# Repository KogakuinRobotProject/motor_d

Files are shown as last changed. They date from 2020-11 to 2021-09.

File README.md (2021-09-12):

# 直流モータドライバ基盤
## 仕様　<br>
to252のFETに対応している。用件によって必要となる定格のFETを使うこと<br>
PWMfreqは20kHz～50kHz(100kHzとかでも動くだろうけど、スイッチング損失えぐい)<br>

|FaultFlag|LEDstate|
|---|---|
|FF1|Green|
|FF2|Red|

<br>

|FF1state|FF2state|MDstate|
|---|---|---|
|0|0|Normal Operation|
|1|0|Overtemperature|
|0|1|Short-to-ground,Short-to-supply,Shorted load|
|1|1|V5 undervoltage,VREG undervoltage,Bootstrap undervoltage|

## FET使用例（FETゲート回路周りの定数）

|MOSFETname|Gate Register|Gate to Source Capasita|
|----|----|----|
|IPD034N06N3G|10|220~1000pF|
|DMTH4005SK3Q|10|1000~2200pF|

## 注意
FETを変えた場合ゲート入力抵抗、GS間容量(C_add)を適切な値に変更すること。目安は下記 <br>
<a href="https://www.codecogs.com/eqnedit.php?latex=\frac{C_{dg}}{C_{gs}&plus;C_{add}}&space;=&space;0.5" target="_blank">\frac{C_{dg}}{C_{gs}+C_{add}} = 0.5</a> <br>
上式で容量を決めたらオシロスコープでFETの立ち下がりを見てセルフターンオンしないゲート入力抵抗を入れる <br>
基板上のC_5,C_6の値をFETの追加容量含んだトータルゲートチャージの10倍ほどのコンデンサに変更する<br>
※データシート上では容量ではなく、充電される電荷が記載されているため、電荷にV_gsを徐算すること<br>
※セルフターンオンしているとDtimeでカバーできない上下アームオン状態が生まれ、短絡しFETの発熱およびドライバの短絡検知、電流制限に引っかかる。<br>
※セルフターンオンであると思っていたものがそうでなかった。低負荷状態ではセルフターンオンの発生は確認できなかったが、高負荷時に発生する可能性があるため上記目安を参考に容量を追加すること。<br>

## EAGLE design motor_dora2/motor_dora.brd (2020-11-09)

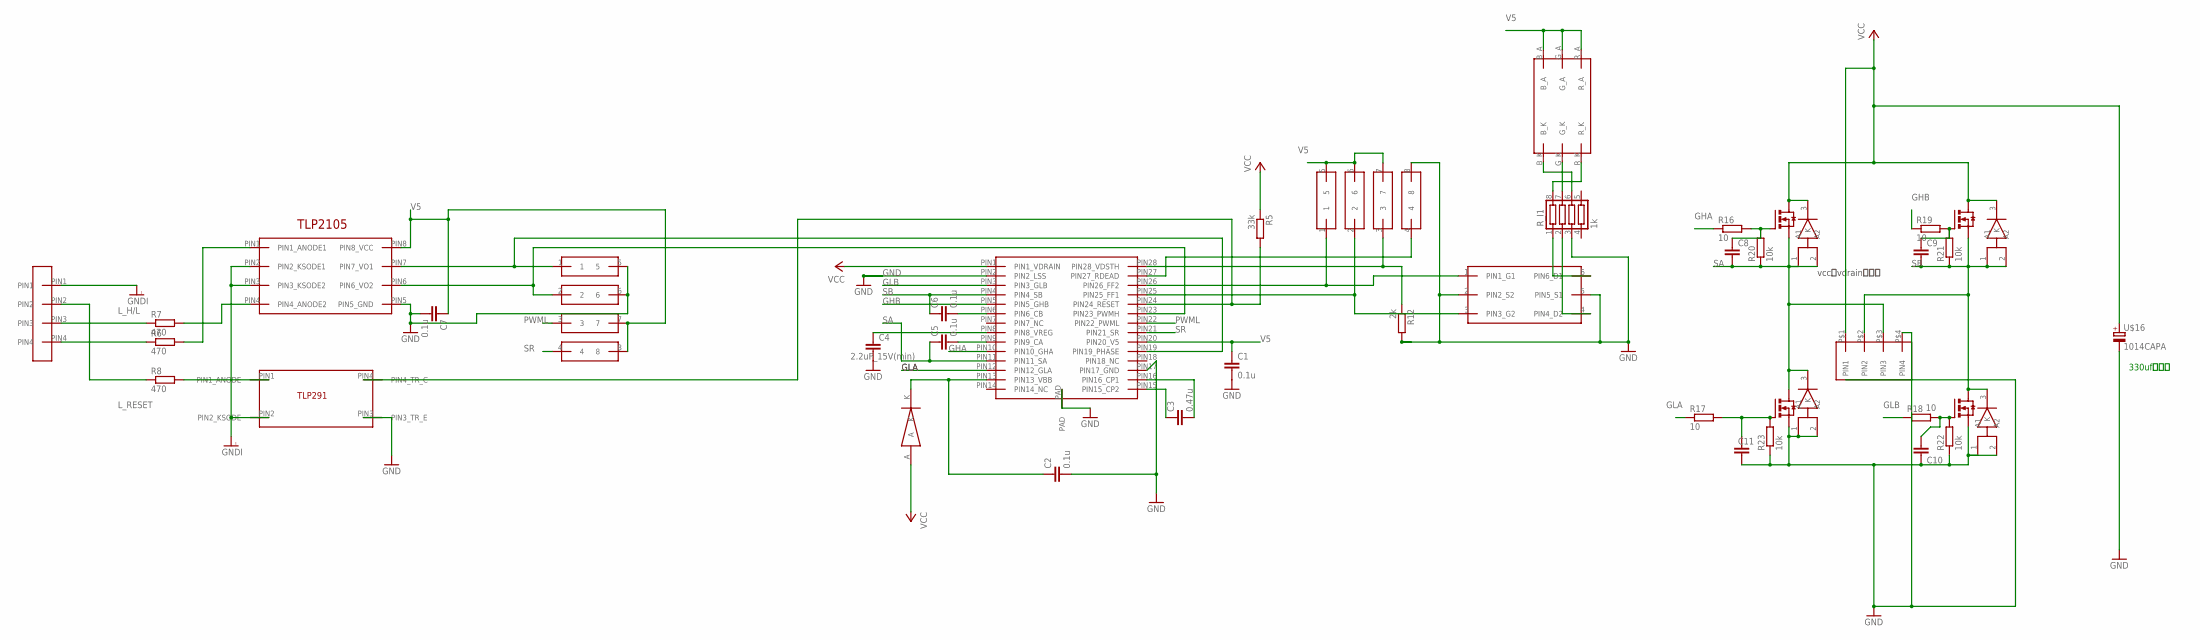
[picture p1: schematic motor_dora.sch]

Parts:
C1, C2, C5, C6, C7: 0.1u; C2012
C3: 0.47u; C2012
C4: 2.2uF_15V(min); C2012
C8, C9, C10, C11: C-EUC2012; C2012
R5: 33k; R2012
R6, R7, R8: 470; R2012
R12: 2k; R2012
R16, R17, R18, R19: 10; R2012
R20, R21, R22, R23: 10k; R2012
R_I1: 1k; 0603X4RESISTOR
U$1: A3921
U$2: TLP2105
U$3: TLP291
U$4: RGB_LED
U$5, U$6: 10k; 1005X4RESISTOR
U$7, U$12, U$15, U$19: SBR10M100P5Q; POWERDI_5
U$8, U$9, U$10, U$11: IPD034N06N3G; TO252
U$13: DF1B_L_4P
U$14: VL_4P
U$16: 1014CAPA
U$17: SMD_DAIOD
U$18: SSOT6_FET

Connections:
GHA: R16.1, U$1.PIN10 (PIN10_GHA)
GHB: R19.1, U$1.PIN5 (PIN5_GHB)
GLA: R17.1, U$1.PIN12 (PIN12_GLA)
GLB: R18.1, U$1.PIN3 (PIN3_GLB)
GND: C1.2, C2.2, C4.2, C7.2, C10.2, C11.2, R12.2, R22.1, R23.1, R_I1.3, U$1.PAD, U$1.PIN2 (PIN2_LSS), U$1.PIN17 (PIN17_GND), U$2.PIN5 (PIN5_GND), U$3.PIN3 (PIN3_TR_E), U$5.5, U$5.6, U$6.8, U$7.1 (A1), U$7.2 (A2), U$10.PIN3 (PIN3_S), U$11.PIN3 (PIN3_S), U$12.1 (A1), U$12.2 (A2), U$14.P$4 (PIN4), U$16.-, U$18.2 (PIN2_S2), U$18.5 (PIN5_S1)
GNDI: U$2.PIN2 (PIN2_KSODE1), U$2.PIN3 (PIN3_KSODE2), U$3.PIN2 (PIN2_KSODE), U$13.PIN1
L_H/L: R7.1, U$13.PIN3
L_RESET: R8.1, U$13.PIN2
unnamed: C2.1, U$1.PIN13 (PIN13_VBB), U$17.K
unnamed: R6.1, U$13.PIN4
unnamed: R6.2, U$2.PIN1 (PIN1_ANODE1)
unnamed: C3.1, U$1.PIN15 (PIN15_CP2)
unnamed: U$1.PIN27 (PIN27_RDEAD), U$6.4
unnamed: R7.2, U$2.PIN4 (PIN4_ANODE2)
unnamed: R5.2, U$1.PIN24 (PIN24_RESET), U$3.PIN4 (PIN4_TR_C)
unnamed: U$1.PIN23 (PIN23_PWMH), U$2.PIN6 (PIN6_VO2), U$5.2
unnamed: U$1.PIN26 (PIN26_FF2), U$6.1, U$18.1 (PIN1_G1)
unnamed: R8.2, U$3.PIN1 (PIN1_ANODE)
unnamed: C3.2, U$1.PIN16 (PIN16_CP1)
unnamed: U$1.PIN25 (PIN25_FF1), U$6.2, U$18.3 (PIN3_G2)
unnamed: C4.1, U$1.PIN8 (PIN8_VREG)
unnamed: R_I1.7, U$4.G_K
unnamed: R12.1, U$1.PIN28 (PIN28_VDSTH), U$6.3
unnamed: C6.2, U$1.PIN6 (PIN6_CB)
unnamed: C5.2, U$1.PIN9 (PIN9_CA)
unnamed: R_I1.2, U$18.4 (PIN4_D2)
unnamed: R_I1.8, U$4.R_K
unnamed: R_I1.6, U$4.B_K
unnamed: R_I1.1, U$18.6 (PIN6_D1)
unnamed: C8.1, R16.2, R20.2, U$8.PIN1 (PIN1_G)
unnamed: C9.1, R19.2, R21.2, U$9.PIN1 (PIN1_G)
unnamed: C11.1, R17.2, R23.2, U$10.PIN1 (PIN1_G)
unnamed: C10.1, R18.2, R22.2, U$11.PIN1 (PIN1_G)
unnamed: U$1.PIN19 (PIN19_PHASE), U$2.PIN7 (PIN7_VO1), U$5.1
PWML: U$1.PIN22 (PIN22_PWML), U$5.3
SA: C5.1, C8.2, R20.1, U$1.PIN11 (PIN11_SA), U$7.3 (K), U$8.PIN3 (PIN3_S), U$10.PIN2 (PIN2_D), U$14.P$3 (PIN3), U$19.1 (A1), U$19.2 (A2)
SB: C6.1, C9.2, R21.1, U$1.PIN4 (PIN4_SB), U$9.PIN3 (PIN3_S), U$11.PIN2 (PIN2_D), U$12.3 (K), U$14.P$2 (PIN2), U$15.1 (A1), U$15.2 (A2)
SR: U$1.PIN21 (PIN21_SR), U$5.4
V5: C1.1, C7.1, U$1.PIN20 (PIN20_V5), U$2.PIN8 (PIN8_VCC), U$4.B_A, U$4.G_A, U$4.R_A, U$5.7, U$5.8, U$6.5, U$6.6, U$6.7
VCC: R5.1, U$1.PIN1 (PIN1_VDRAIN), U$8.PIN2 (PIN2_D), U$9.PIN2 (PIN2_D), U$14.P$1 (PIN1), U$15.3 (K), U$16.+, U$17.A, U$19.3 (K)

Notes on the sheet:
vccとvdrainは同じ
330ufつけて

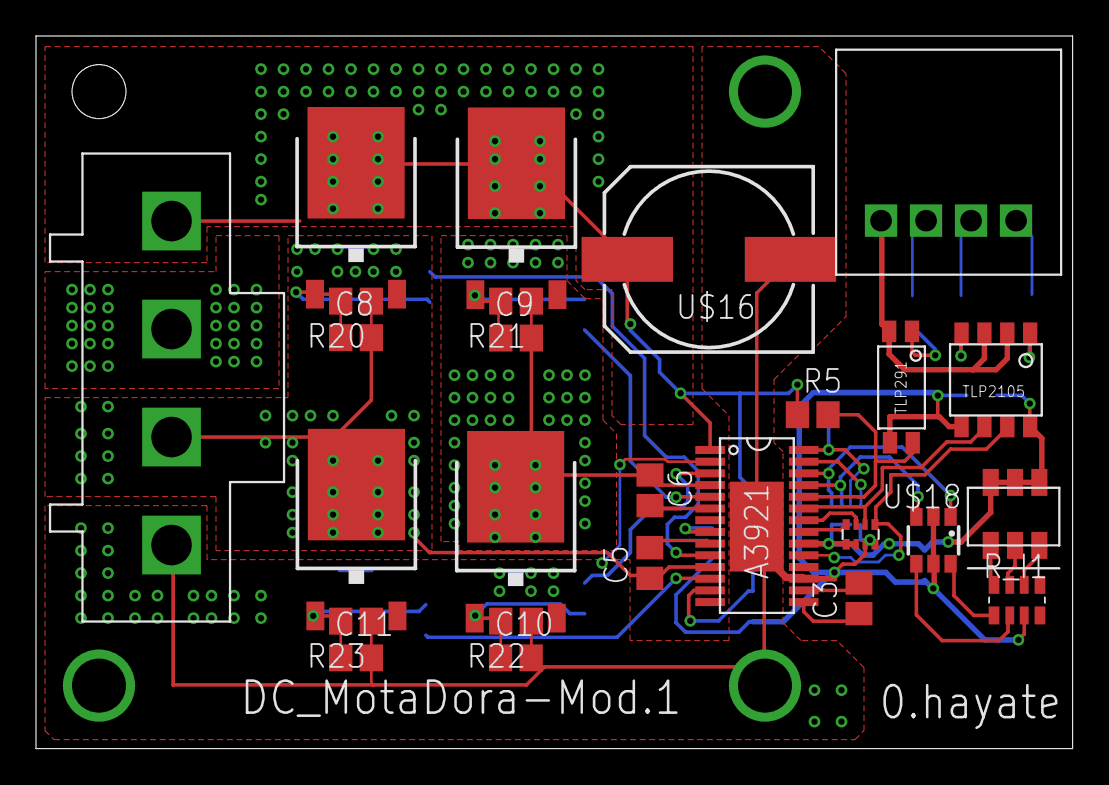
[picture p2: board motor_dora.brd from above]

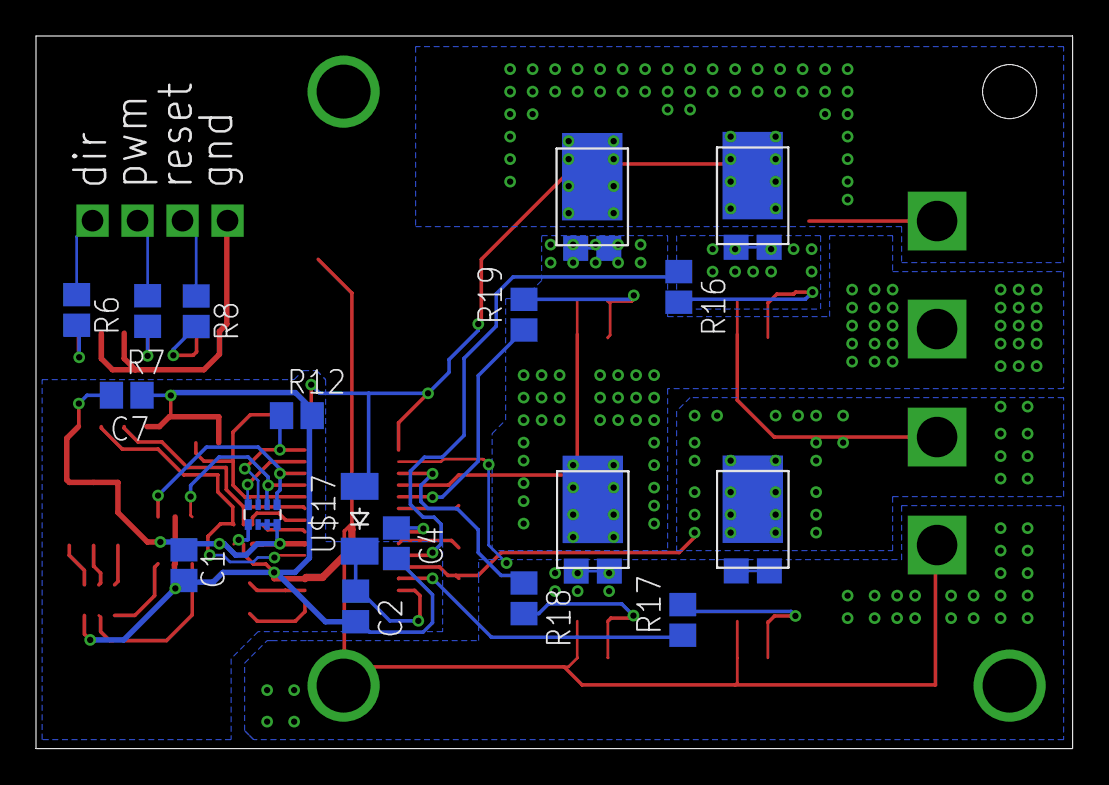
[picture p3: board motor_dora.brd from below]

Board: 2 copper layers, 57.6 x 39.6 mm, 44 parts (18 on the bottom side), 40 nets.

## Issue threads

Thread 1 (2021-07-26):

FET、集合抵抗のシンボルの変更をしといて

hayate2718, 2021-07-26:
FETがNP52N06SLGが使われたままで紛らわしいと思うので、気になってる人いれば直しとくと良いと思います。
集合抵抗のシンボルが最新のライブラリのシンボルと異なるので変えておくといいと思います。
旧シンボルだとvalueが図面上でシンボルを選択しないとわからないので。
最後にreademeを作ってFETを任意のものに変更しやすいようにしたので参考にしてください

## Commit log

2020-09-23 改良型モタドラ
    部品点数の低下、基板サイズの低下が行われた。
    [motor_dora.brd, motor_dora.sch]
2020-09-24 ゲート駆動を調整
    [motor_dora.brd, motor_dora.sch]
2020-11-09 pwm入力をプルダウンにした
    [motor_dora.brd, motor_dora.sch]
